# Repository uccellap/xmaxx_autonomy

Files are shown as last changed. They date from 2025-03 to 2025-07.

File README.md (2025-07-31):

# xmaxx_autonomy
The purpose of this repo is to provide documentation on the consutrction of an autonomous platform using the Traxxas XMAXX platform as a base.

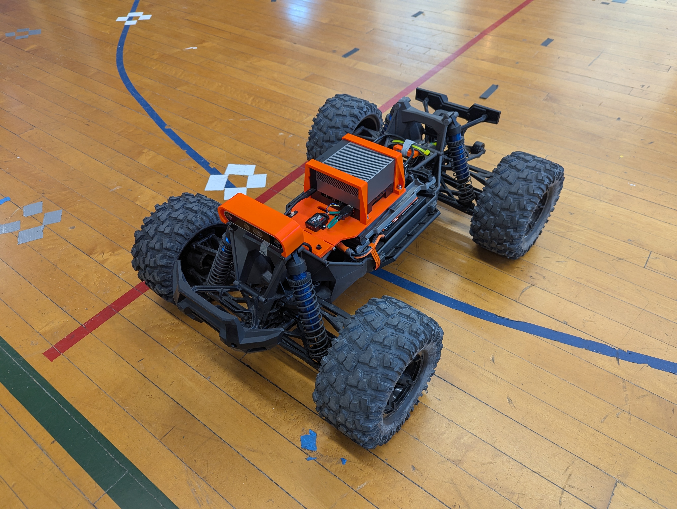
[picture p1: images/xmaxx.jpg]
xmaxx


This is very much a *work in progress*.

## Platform Parts List (Main)
| Part  | Description | Link | Cost Estimate |
| --- | --- | --- | --- |
| Traxxas XMAXX 8s | Base RC platform | https://traxxas.com/products/landing/x-maxx/ | $1099.95 |
| Castle Mamba X 8S 33.6V ESC W /1717-1260KV Sensored Motor | Replacement ESC and sensored motor for telemetry and low-speed control | https://www.castlecreations.com/en/1-6th-scale/mamba-monster-x-8s-33-6v-esc-w-1717-1260kv-sensored-motor-010-0165-03 | $389.95 |
| M2C Racing 110 X Series Motor Mount | Mount to install new motor in XMAXX | https://m2cracing.net/shop/shop.php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 | $108.72
| Castle Serial Link | Provides telemetry and control via serial | https://www.castlecreations.com/en/serial-link-010-0121-00 | $76.50 |
| Castle Link V3 USB Programming Kit | Used to set configuration on the ESC | https://www.castlecreations.com/en/castle-link-v3-usb-programming-kit-011-0119-00 | $21.95 |
| RadioMaster MT12 Surface Radio Controller (ERLS) | Manual ERLS RC controller | https://www.radiomasterrc.com/collections/surface-radio/products/mt12-surface-radio-controller | $129.99 |
| RadioMaster ER6 2.4GHz ELRS PWM Receiver | Receiver and controller that will be flashed with custom ERLS autonomy firmware | https://www.radiomasterrc.com/collections/receivers/products/er6-2-4ghz-elrs-pwm-receiver | $24.99 | 
| Smart Powerstage 8S Surface Bundle: (2) G2 5000mAh 4S LiPo IC5 & S2100 Charger | Batteries and charger | https://www.spektrumrc.com/product/smart-powerstage-8s-surface-bundle-2-g2-5000mah-4s-lipo-ic5-and-s2100-charger/SPMXPSS850.html | $354.99 |
| Spektrum Connector IC5 | Batter connector to be soldered onto ESC wires | https://a.co/d/7pLiS2Y | $11.99 |

** Unfortunately, the replacement motor requires some physical alterations to the XMAXX plastic chassis to fit.  Hence a dremel will be necessary to remove two supports, and cut away some material on the stock gear mesh cover.  It's not ideal, but there does not seem to be a sensored motor with telemetry that fits in the stock slot without mods.  If this is a show stopper, another possible chassis is the Arrma Kraton (https://www.arrma-rc.com/en/product/1-5-kraton-8s-exb-avc-4x4-rtr-brushless-speed-truck-black/ARA5808V2T1.html).  It looks like the standard motor mount on this platform would take the new motor without modification - but this has not yet been investigated. The platform sits a bit lower, and a new mount would need to be designed. **

## Platform Parts List (Sensors)
| Part  | Description | Link | Cost Estimate |
| --- | --- | --- | --- |
| Intel Realsense D456 | Depth vision camera | https://store.intelrealsense.com/buy-intel-realsense-depth-camera-d456.html | $469.00 |
| Microstrain 3DM-GX5-25 | AHRS IMU (Optional - D456 has internal IMU but competes for USB bandwidth) | https://www.microstrain.com/inertial-sensors/3dm-gx5-25 https://www.mouser.com/ProductDetail/MicroStrain-by-HBK/3DM-GX5-AHRS-40G-900-DPS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 | $2045.38 |
| SparkFun GNSS-RTK L1/L5 Breakout - NEO-F9P | L1/L5 GPS w/USB interface | https://www.sparkfun.com/sparkfun-gnss-rtk-l1-l5-breakout-neo-f9p-qwiic.html | $249.95 |
| GNSS L1/L5 Multi-Band High Precision Antenna - 5m (SMA) | L1/L5 GPS antenna | https://www.sparkfun.com/gnss-l1-l5-multi-band-high-precision-antenna-5m-sma.html | $60.00 |

** Instead of the AHRS/IMU/GPS setup above, this could be replaced by something like the VectorNav VN-300 (https://www.vectornav.com/products/detail/vn-300) - although these are not cheap: ~5K (https://www.vectornav.com/store/products/dual-gnss-ins/p/vn-300-rugged-dual-gnssins) **

## Platform Parts List (Compute)
| Part  | Description | Link | Cost Estimate |
| --- | --- | --- | --- |
| Jetson AGX Orin 64GB Developer Kit | GPU Compute | https://www.arrow.com/en/products/945-13730-0050-000/nvidia?nvid=em-945-13730-0050-000 | $1999.00 |
| SAMSUNG 990 PRO SSD 2TB | Storage for Orin - Many options here | https://a.co/d/33MjdJy | $179.99

## Platform Parts List (Wires and Connectors)
| Part  | Description | Link | Cost Estimate |
| --- | --- | --- | --- |
| GH1.25 to Dupont2.54 Pre-Crimped Cables and Connectors Kit Compatible with JST GH 1.25mm for Pixhawk4 Pixhawk 6C 6X 20cm Silicone Wire | Wire kit for cable from ER6 to Orin | https://a.co/d/4mtFtRP | $19.99 |
| M3 / M4 Nuts and Bolts | Connecting all the things - something like this at Amazon | https://a.co/d/4Z7bRa4 | $9.99 |
| 50mm M3 Bolts | You'll need 2 of these for the hinge - something like this at Amazon | https://a.co/d/0kqJr4s | $7.99 |
| M4 rubber washers | These are for spacing with the main mount - something like this at Amazon | https://a.co/d/5ORINJq | $7.99 |
| EC5 Male to XT60 Female Adapter | Battery cable to Orin | https://a.co/d/8FEJKTv | $9.99 |
| XT60 Male to Male DC 5.5mm x 2.5mm Cable | Batter cable to Orin | https://a.co/d/5boBf6K | $10.99 |
| Right angle USB-C adapter | For D456 cable - something like this on Amazon | https://a.co/d/9OtB0vA | $8.61 |
| High quality USB-C to USB-C cable for D456 | Something like this on Amazon | https://a.co/d/47YHbUF | $25.99 |
| USB-C to USB-A for GPS connection | Something like this on Amazon | https://a.co/d/cIZYpWn | $5.99 |
| 20awg RC wire | Something like this on Amazon - will be cut up | https://a.co/d/dIKhoX0 | $14.99 |
| Spectrum XBC100 Smart Battery Checker | Optional | https://a.co/d/jaZsQSk | $44.99 |
| Spektrum IC5 to IC3 Adapter | Optional - for battery tool | https://a.co/d/ib37hAt | $14.99 |
| Velcro Wraps | These are helpful - something like this on Amazon | https://a.co/d/88yIFMP | $10.81 |
| Microstrain short cable | Optional if you want to build a shorter cable for the Microstrain | https://www.mouser.com/ProductDetail/MicroStrain-by-HBK/MICRO-DB9-LEADS?qs=DPoM0jnrROVExKPQkf4YSQ%3D%3D | $75.97 |
| Microstrain short cable USB | Optional if you want to build a shorter cable for the Microstrain | https://a.co/d/herxRRp | $6.88 |

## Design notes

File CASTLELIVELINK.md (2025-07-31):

# XMAXX Autonomy CastleLink <---> ELRS Setup

## Flash and Configure Firmware

### Flash custom firmware to the ER6
- The ER6 will need to be powered up.  This can be done by using the ESC directly (just plugging in to any of the ports), or by otherwise providing ~5.5V.
- Power up the ER6 and wait for ~30s. It should start a wireless AP with SSID 'ExpressLRS RX'.  The password is 'expresslrs'
- Go the the configuration page at http://10.0.0.1
- Go to the 'update' page and upload and flash the firmware image `RM_ER6_ERLS_RX_firmware/firmware_Unified_ESP32_2400_RX_via_UART.bin`

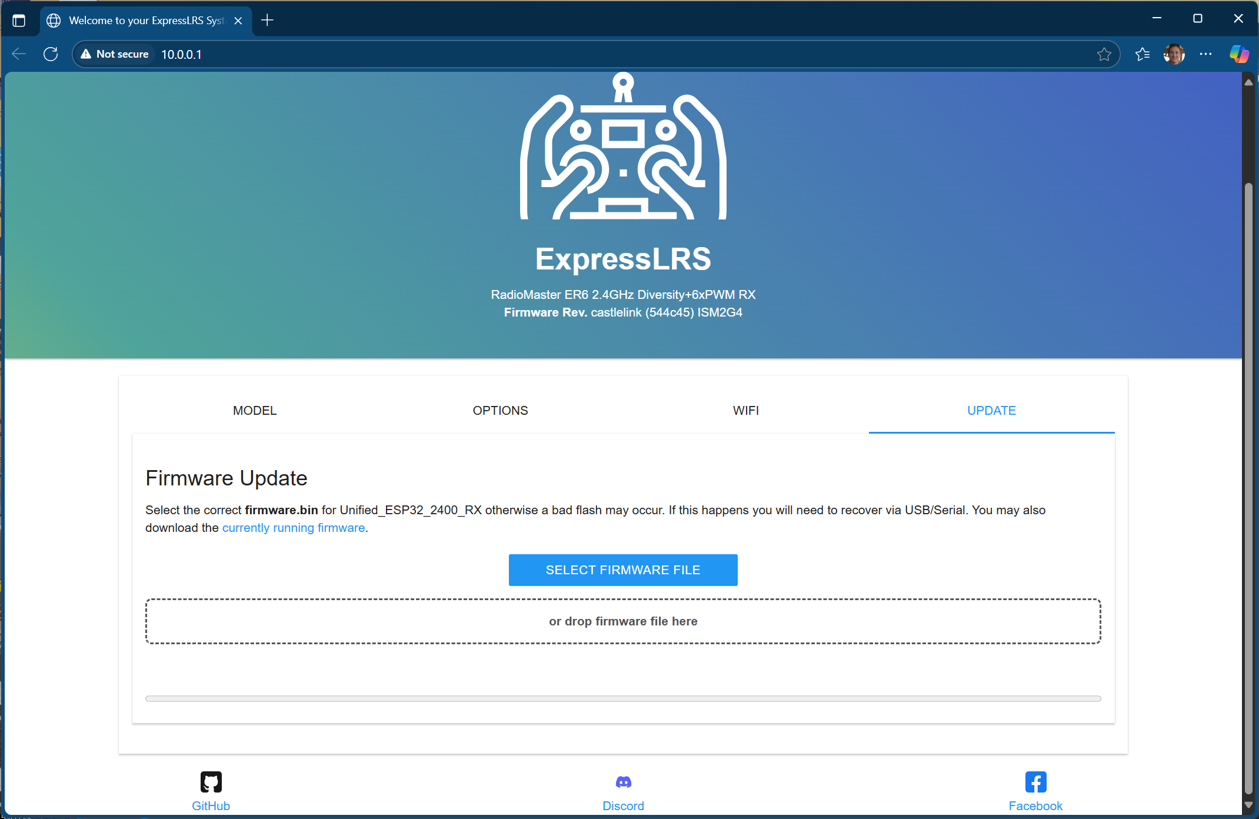
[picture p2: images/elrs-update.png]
update screen


- Reboot and reconnect
- Change the configuration to match the following:
- **Model**

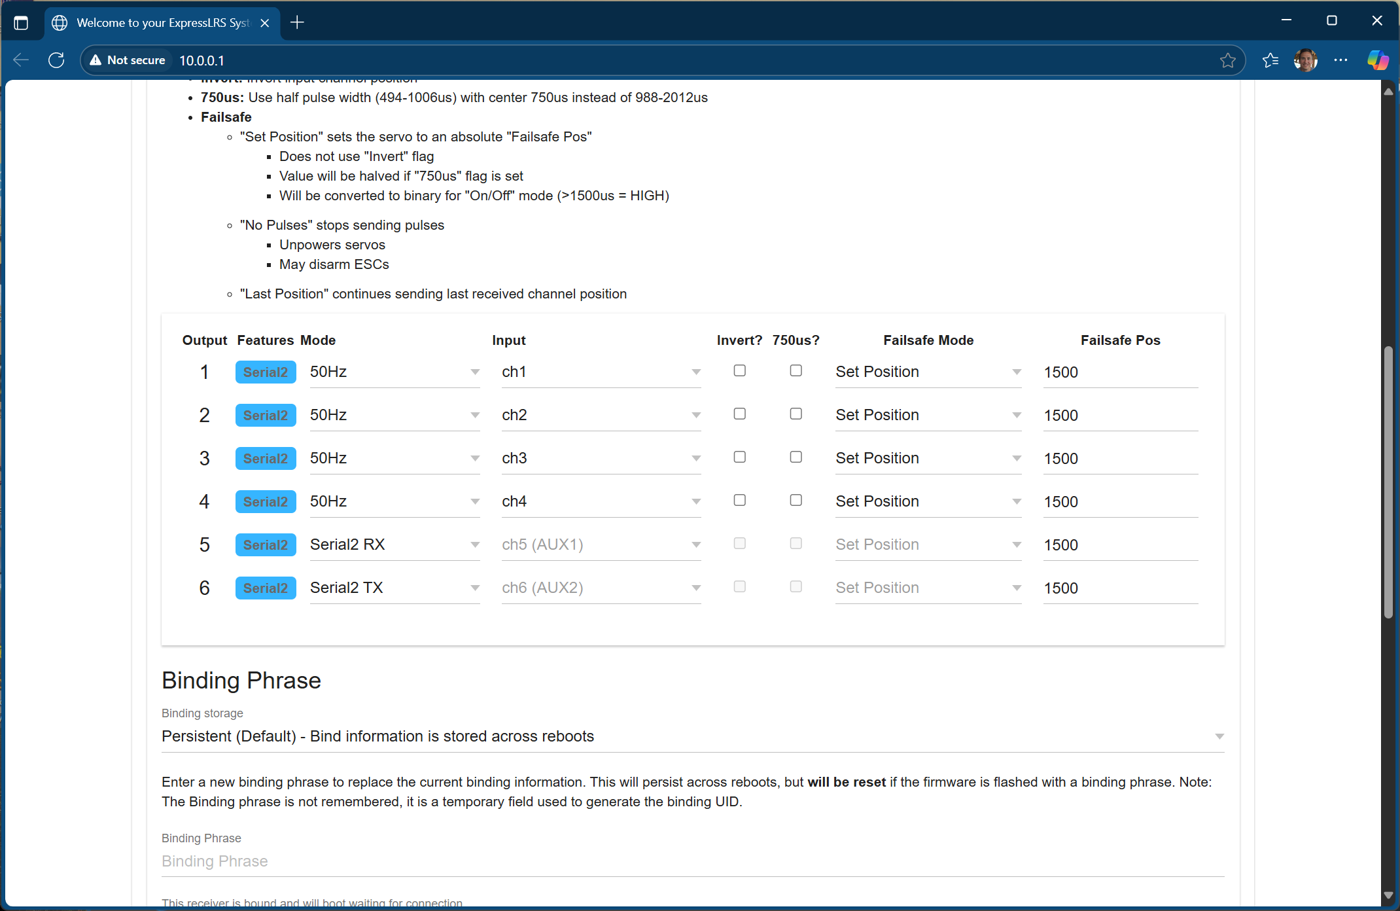
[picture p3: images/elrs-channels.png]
channels screen


- *Note that the RX and TX here should correspond to the Serial Link TX and RX (e.g. RX-->TX, TX-->RX)*

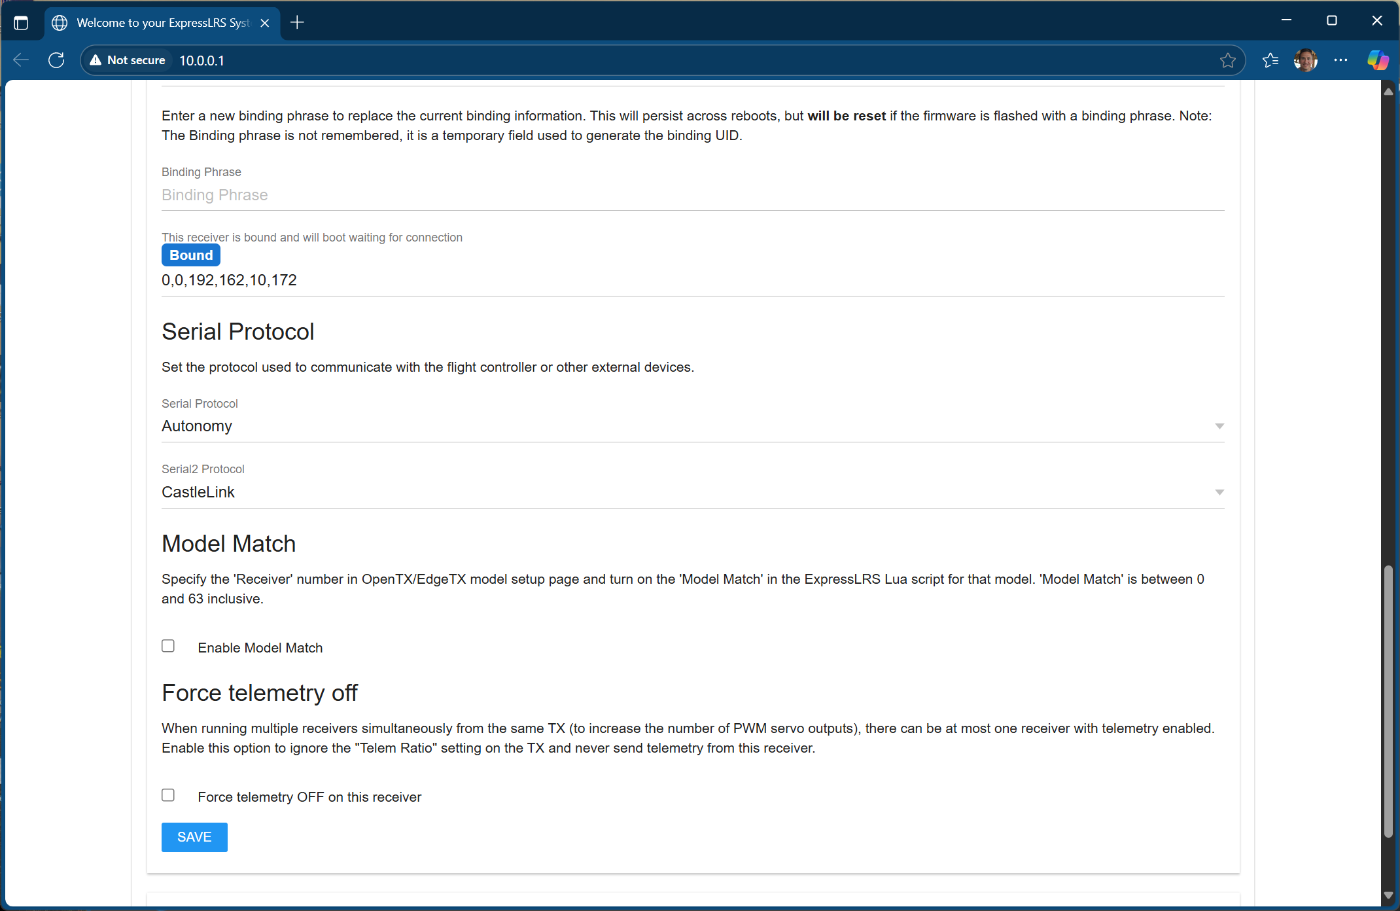
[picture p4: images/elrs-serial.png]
serial screen


- **Options**

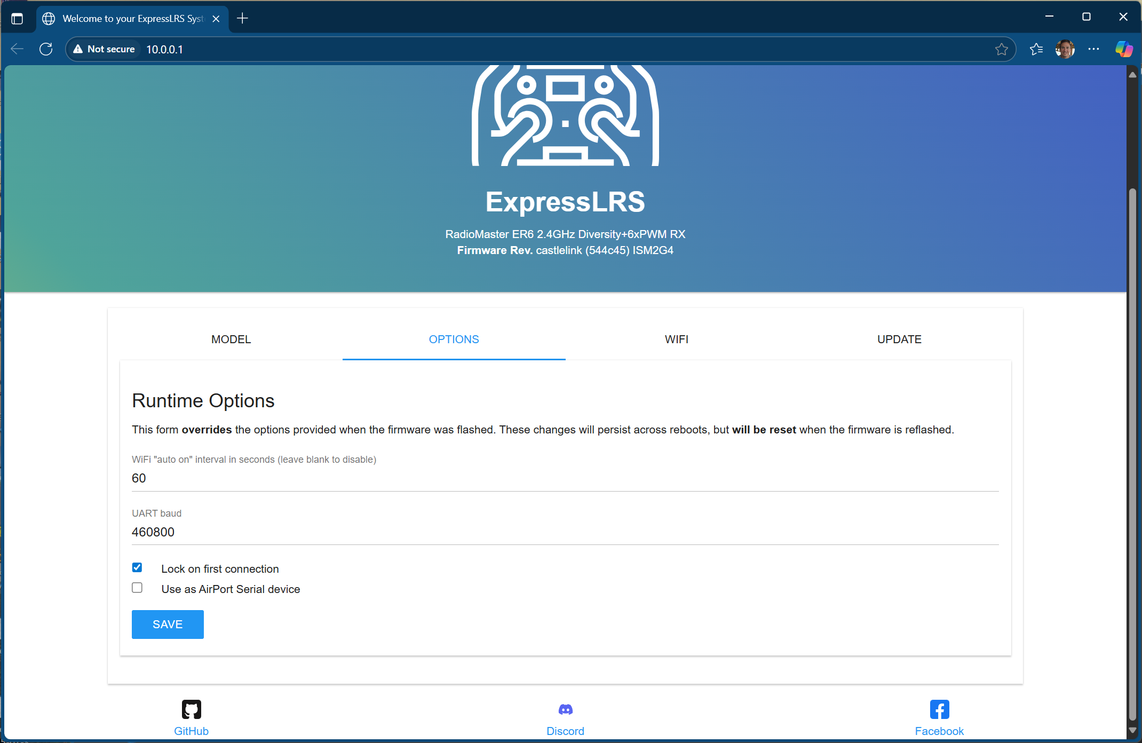
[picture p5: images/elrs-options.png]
options screen


- Save the configuration

### Update the ESC Configuration
- Using the CastleLink USB adapter, configure the ESC using  **CastleLink 2** available here: [https://home.castlecreations.com/download-castle-link]
- Make the following configuration changes
- **Basic**

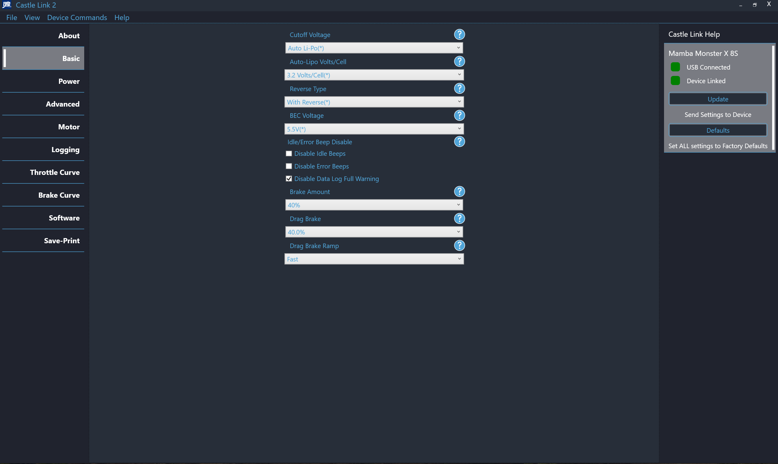
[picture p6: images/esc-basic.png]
basic screen


- **Power**

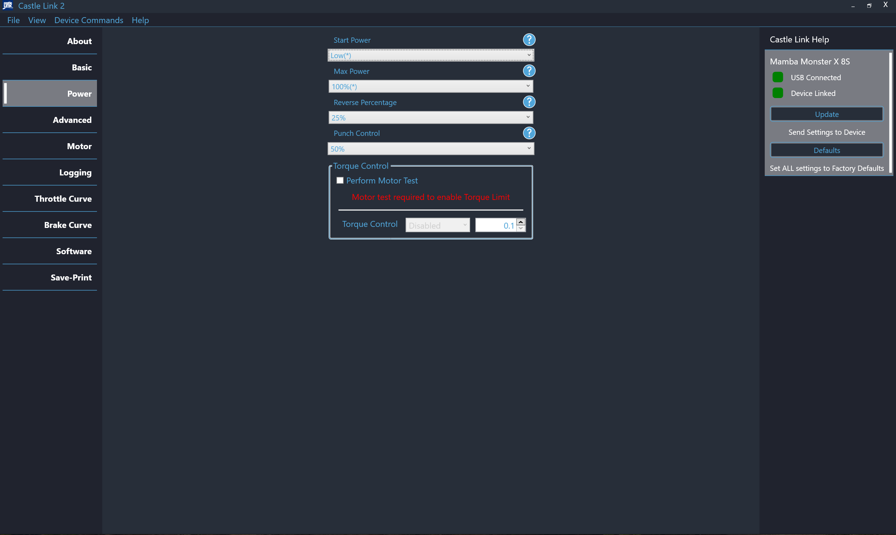
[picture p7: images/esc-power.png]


- **Advanced**
- This is critical as it is what enables LiveLink between the ESC and the SerialLink board

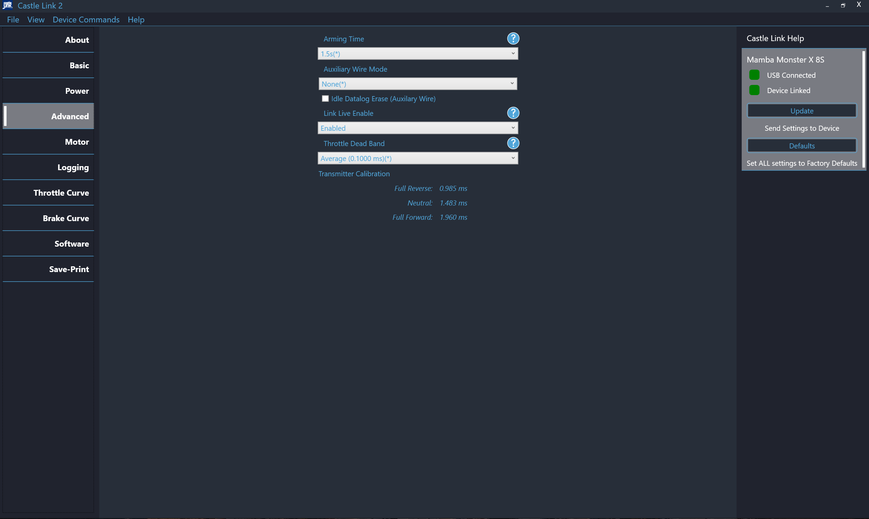
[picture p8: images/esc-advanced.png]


### Update the SerialLink Configuration
- Using the CastLink USB adapter, configure the SerialLink board using **CastleLink Classic** available here: [https://home.castlecreations.com/download-castle-link]
- Make the following configuration changes

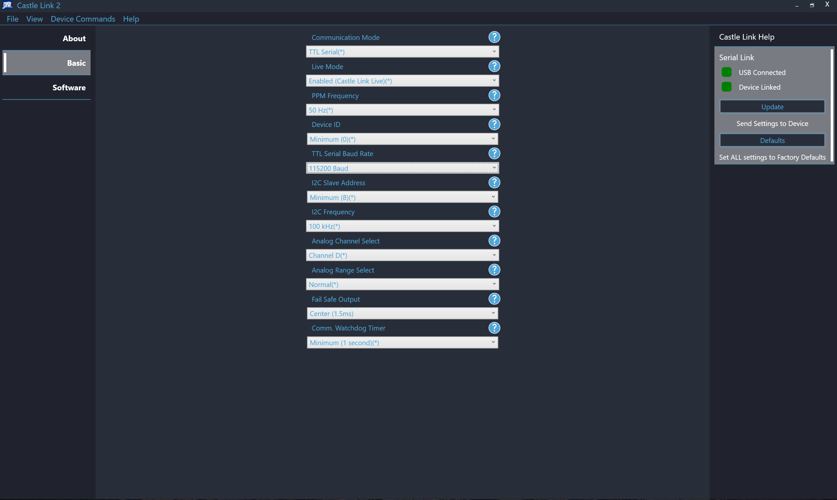
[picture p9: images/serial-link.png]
serialink screen


- *Note CastleLink 2 (shown in the image) is able to read the configuration, but is not able to write it (despite appearing to do so in the UX).  CastleLink Classic is necessary to successfully write the config.*

## Wire up the hardware

- Ultimately, the ESC connects to the SerialLink board via the standard 3-wire cable (and talks the LiveLink protocol).
- The SerialLink then connects to the ER6 via a UART.
- The ESC provides power to both the SerialLink board and the ER6 - **as well as the steering servo**.
- As such, although the SerialLink board has a +V on the 'ER6 side', the +V traces in the board cannot carry enough current to keep the steering servo happy.  So you will need to add a wire from the 'ESC side' +V to any of the +V lines on the ER6.
- From the 'ER6 side' of the SerialLink, you will need to wire, RX, TX, and GND over to the ER6.
- On the ER6, it should look like this:

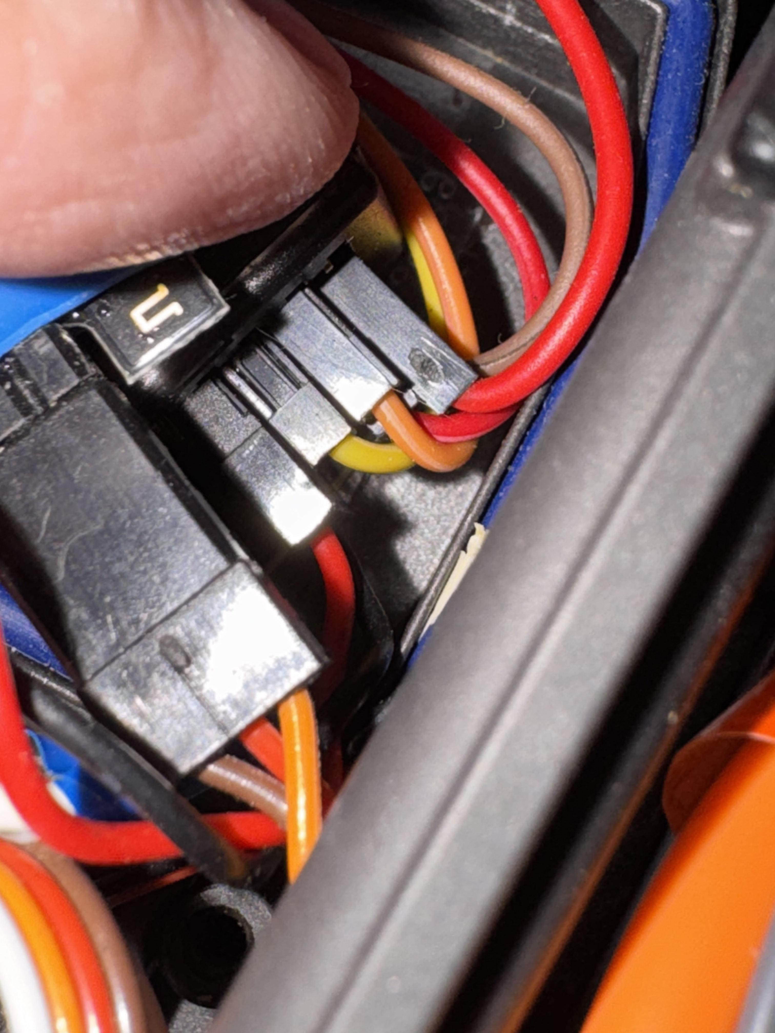
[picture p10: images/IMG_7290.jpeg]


- Far right, Power (extra wire from +V 'ESC side' of the SerialLink) and GND from the SerialLink
- Next, Port 6 signal, ER6 TX, SerialLink RX (orange in the pic)
- Next, Port 5 signal, ER6 RX, SerialLink TX (yellow in the pic)
- Next - Port 4, ESC fan power - ignore if you don't have a fan

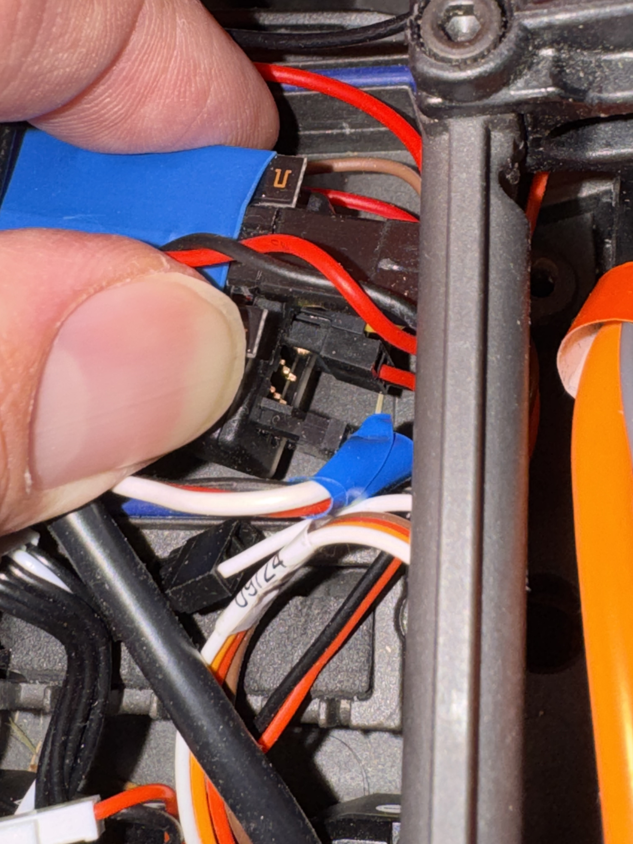
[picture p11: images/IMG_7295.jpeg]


- Finally, Port 1 - steering servo

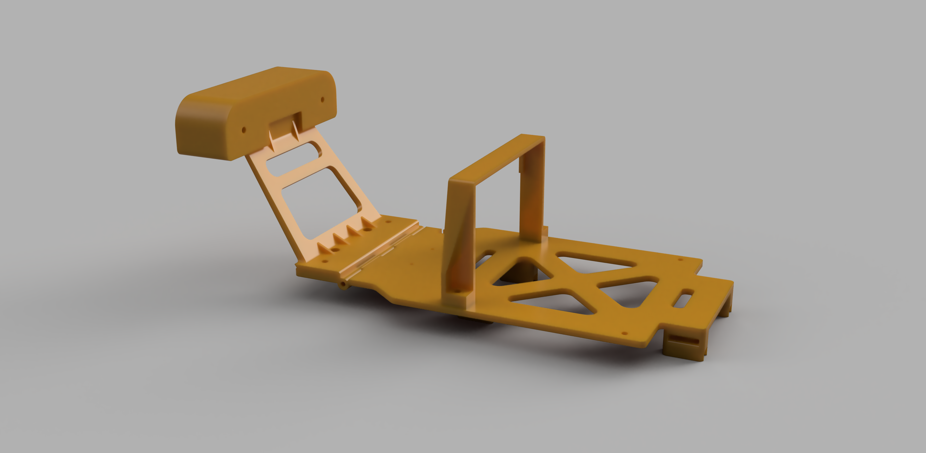
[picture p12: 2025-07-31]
3d_model/xmaxx_v18.png

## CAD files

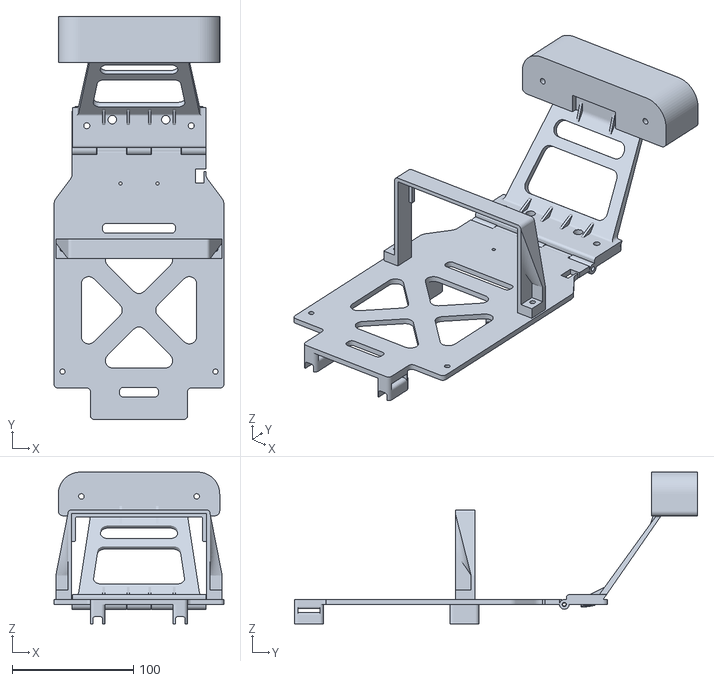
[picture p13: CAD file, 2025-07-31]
3d_model/xmaxx v18.stl
140.0 x 332.0 x 125.0

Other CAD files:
3d_model/xmaxx v18.f3d

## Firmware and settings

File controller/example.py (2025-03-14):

import serial
import time
import threading
import struct
from struct import Struct

#-------------------------------------------
"""
// Defines
//----------------------------------------------------
// API
#define AUTONOMY_API_MAGIC         (0x5A5A5A5A)
#define AUTONOMY_API_VERSION       (0x01)
#define AUTONOMY_CMD_TYPE_DRIVE    (0x01)
#define AUTONOMY_DATA_TYPE_TELEM   (0x81)

// Types
//----------------------------------------------------
typedef struct __attribute__((packed)) {
    int16_t     throttle;       // 1000-1500-2000
    int16_t     steering;       // 1000-1500-2000
} AutonomyDriveCmd_t;

typedef struct __attribute__((packed)) {
    uint32_t    magic;
    uint8_t     version;
    uint8_t     type;
    uint8_t     crc;
    union {
        AutonomyDriveCmd_t drive;
    } msg;
} AutonomyCmd_t;

typedef struct __attribute__((packed)) {
    uint64_t    counter;
    uint8_t     state;
    uint16_t    rcThrottle;     // 1000-1500-2000
    uint16_t    rcSteering;
    uint16_t    rcSwitchA;
    uint16_t    rcSwitchB;
    uint16_t    rcSwitchC;
    uint16_t    rcSwitchD;
    uint16_t    acThrottle;
    uint16_t    acSteering;
    uint8_t     upRssi;
    uint8_t     upLqi;
    uint8_t     downRssi;
    uint8_t     downLqi;
    uint16_t    escVoltageRaw;
    uint16_t    escCurrentRaw;
    uint16_t    escRpmRaw;
    uint16_t    escTempRaw;
} AutonomyTelemetryData_t;


// note - these are close enough that we won't
// bother with variable length structs
typedef struct __attribute__((packed)) {
    uint32_t    magic;
    uint8_t     version;
    uint8_t     type;
    uint8_t     crc;
    union {
        AutonomyTelemetryData_t telem;
    } msg;
} AutonomyData_t;
"""

#-------------------------------------------
MsgHeader = Struct('<LBBB')
MsgTelem  = Struct('<QBHHHHHHHHBBBBHHHH')

MsgDrive  = Struct('<LBBBHH')

#-------------------------------------------
def crc8(data):
    c = 0
    for i in range(len(data)):
        c ^= data[i]
        for j in range(8):
            if(c & 0x80):
                c = ((c << 1) ^ (0x1e7))
            else:
                c = (c << 1)
    return c

#-------------------------------------------
def readThread(ser):
    sync = False

    try:
        while True:
            header = bytearray()
            if sync:
                header = ser.read(MsgHeader.size)
            else:
                message = ''
                while not sync:
                    b = ser.read(1)
                    if(b == b'Z'):
                        header.extend(b)
                        if(header == bytearray(b'ZZZZ')):
                            header.extend(ser.read(MsgHeader.size-4))
                            print("[-] MSG: ", message)
                            print("[-] Got sync...")
                            sync = True
                    else:
                        try:
                            message += b.decode()
                        except:
                            pass
                        header = bytearray()

            # unpack header
            msg = MsgHeader.unpack(header)
            msg_magic = msg[0]
            msg_version = msg[1]
            msg_type = msg[2]
            msg_crc = msg[3]

            if msg_magic != 0x5A5A5A5A:
                print("[!] Bad magic")
                sync = False
                continue

            if msg_version != 0x01:
                print("[!] Bad version")
                sync = False
                continue

            # read body
            # all messages are the size of the largest (union)
            body = bytearray()
            body.extend(ser.read(MsgTelem.size))

            # check CRC
            msg = MsgHeader.pack(msg_magic, msg_version, msg_type, 0)
            computed_crc = crc8(msg+body)

            if msg_crc != computed_crc:
                print("[!] Bad CRC")
                sync = False
                continue

            # telem
            if msg_type == 0x81:
                telemMsg = MsgTelem.unpack(body)
                print("[-] telem : {}".format(telemMsg))            


    except Exception as e1:
        print("[!] Error: " + str(e1))

#-------------------------------------------
def setupSerial():
    ser = serial.Serial()
    ser.port = "/dev/cu.usbserial-0001"
    ser.baudrate = 460800
    ser.bytesize = serial.EIGHTBITS
    ser.parity = serial.PARITY_NONE
    ser.stopbits = serial.STOPBITS_ONE
    ser.timeout = None
    ser.xonxoff = False
    ser.rtscts = False
    ser.dsrdtr = False
    ser.writeTimeout = None

    try: 
        ser.open()
    except Exception as e:
        print("error opening serial port: " + str(e))
        return None

    return ser

def main():
    print("[-] XMAXX Interface Startup")
    ser = setupSerial()

    if ser is not None:
        rt = threading.Thread(target=readThread, args=(ser,))
        rt.start()

        while(True):
            time.sleep(1.0/30.0)
            
            """
            print("[-] Issuing test command...")
            msg = MsgDrive.pack(0x5A5A5A5A, 0x01, 0x01, 0x0, 1111, 2222)
            calculated_crc = crc8(msg)
            msg = MsgDrive.pack(0x5A5A5A5A, 0x01, 0x01, calculated_crc, 1111, 2222)
            ser.write(msg)
            ser.flush()"
            """
            
        rt.join()

    if ser:
        ser.close()
    return

if __name__ == '__main__':
    main()
